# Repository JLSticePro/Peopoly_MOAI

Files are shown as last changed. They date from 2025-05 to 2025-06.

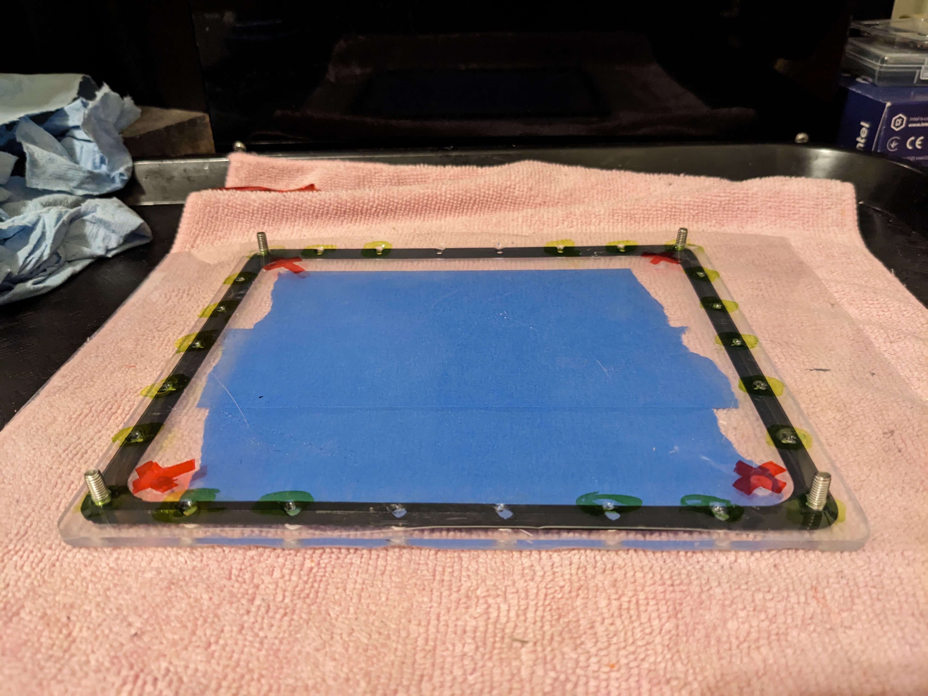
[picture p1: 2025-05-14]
Moai Vats/Printable FEP Vat with acrylic plate/Photos/Plate Ring FEP with 16mm corner screws.jpg

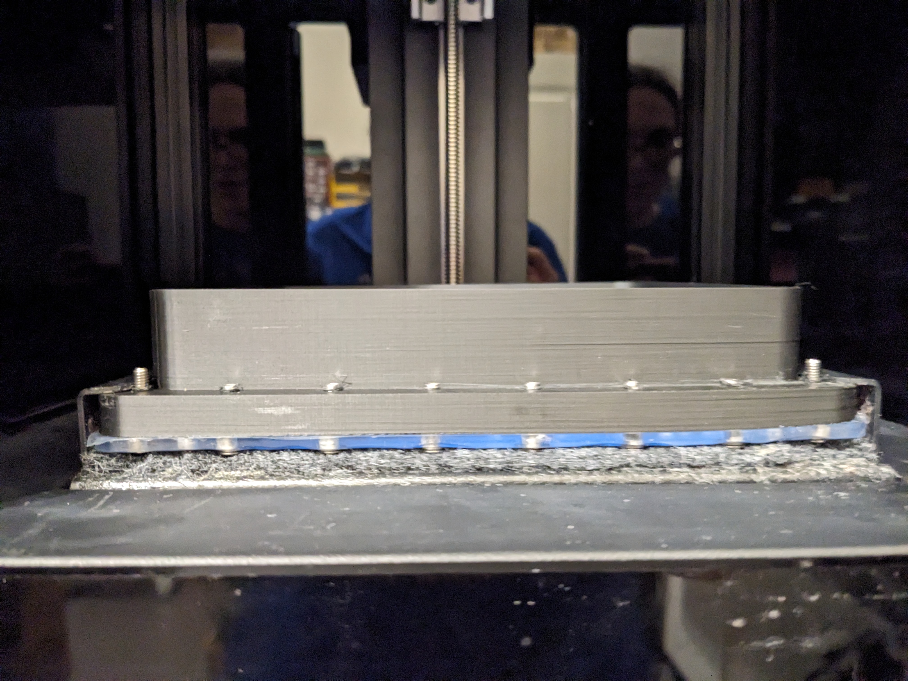
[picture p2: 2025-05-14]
Moai Vats/Printable FEP Vat with acrylic plate/Photos/A warped printed vat can not be used.jpg

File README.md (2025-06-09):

**MOAI MODEL WORK-FLOW:**
- Use ChituBox or LycheeSlicer for arranging and supporting your models.
- Export your arranged and supported model as an OBJ file.
- Open the file in MeshMixer or OrcaSlicer and repair the model
- Export the object as a new STL file. (Cura often fails with OBJ files)
- Slice using CURA 4.7 with the profiles that are included in this repository.
- Save the gcode file to the "gcode" folder on the SD card and put into the Moai.
- In "SETUP "advanced_setting" set the "XY Speed Set" for the cure speed of the resin. (Print-speed Multiplier)

**2025-06-07 New Cura Profiles** -JLS

**2025-06-05 New High-Volume Printable Film Vat** -JLS

**2025-05-11 Initial Commit** -JLS
This repository holds all cumulative files for the MOAI Laser SLA printer. 
This includes all current projects and previous developer files, provided by Peopoly, as the developer no longer works at the company and they are no longer hosting the repository. 
Files over 100MB have been removed from the older repository to meet the 100MB standard push limits, these files are older software and slicer installers.

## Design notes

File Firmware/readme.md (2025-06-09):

** ** Firmware Notes ** **

**MOAI Firmware Firmware FULL CHANGELOG (Peopoly Dev)**

V.18 (Beta4)
increase Z Follow value to allow higher up movement

V.18 (Beta3)
set PM reset distance = 0 to disable PM motor
set Zfollow to negative value for up movement

V.18 (Beta2)

V.18 (Beta)
Setting definition change
Z-Follow 0-60 each unit represents 0.1mm the range of value is (-1) to (5)
Z-Follow 0 = -1 mm movement upward during peel
Z-Follow 60 = 5 mm movement downward during peel
For recommended z-follow for general printing, it is now 30 (2mm downward movement)

New commands:
M1001 X40 ;laser power change to 40
M1002 X5 ;wait for 5 seconds before continuing
M1003 X1800 ;moving build platform arm to z-axis reset spot of 1800 (in the setting) or 180mm down from the top
M1004 X50 ;peel motion 50 has no meaning
M1005 X10 ;change Pm moto speed to 10
M1006 X3 ;change Z Motor Speed to 3
M1007 X12 ;change Z Follows (distance) to 12
M1008 X15 ;change PM Reset Position to 15
M1009 X0 ;Set HE2 port LOW -- X1 ;Set HE2 port High
M1010 X0 ;Set HE3 port LOW -- X1 ;Set HE3 port High

V1.18
Print Duration
Updated default print values
Updated calibration adjustment
Update SD card read i/o.  please print directly from root directory instead of gcode directory.
Initial layers peel speed

V1.16 changelog 2018.3.15
Compensate X/Y
This adjust X/Y for distortions.  Since Galvo/laser setup only has distorion on Y-axis, adjustment to Y-axis is only needed.
Default value for Compensate X is 100
Default value for Compensate Y is 195
Rest of settings are consistent to Firmware 1.15

V1.15 changelog 20171122 
Allow finer calibration and leveling
- X / Y Size range increase from 400 to 1000.  What was 360 is now 900
- Default recommended value is set. Laser is at 58. PM and Z follow motor speed has been reduced as well as Tilt distance
- Laser does not fire when user adjust value in the setting
- User can now immediately cancel a print and it will followed with a peel action before raising the build plate to reduce peel force

V1.14 changelog 2017.09.25 
Allow finer calibration and leveling
- X / Y Size range increase from 100 to 400.  What was 90 is now 360
- Z Reset Position range, increase from 200 to 2000.  What was 188 is now 1880
- Z-follow can now be 0

V1.1x
>enter settings,  XY size is 4 times of recorded value. Z Reset Position is 10 times of the recorded value. Make sure you updated everything to recorded settings

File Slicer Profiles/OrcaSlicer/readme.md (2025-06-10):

**Peopoly Moai for OrcaSlicer**

(Do once - All) Import the "Peopoly_Moai.orca_printer" file into OrcaSlicer
(Do once - Linux or Mac) Copy "Peoploly_Moai_gCode_Processor.py" into your OrcaSlicer "Resources" folder
(Do once - Linux or Mac) Open OrcaSlicer, add the path to the .py script in "Process" "Others" "Post-processing Scripts" for the solid and hollow profiles, then save the profiles. Orcaslicer will process the gcode automatically when you export the gCode file.
(Do once - MS Windows) Install Python to Windows. Copy "Peoploly Moai gCode Processor.py" into your gCode or models folder.

**Work-Flow:**
For most resin-type models:
- Arrange, support, and hollow your models in a resin tool such as LycheeSlicer or ChituBox 
- Export the model as an .obj or .stl file
- Import the model into OrcaSlicer onto the Moai plate
- RUN "FIX MODEL" as the resin tools leave broken non-manifold edges.
- Choose solid profile if you pre-hollowed the model
- Choose hollow profile for regular FDM models, or chunky models directly on the plate. 
- Slice the model and review
- Save the gCode to a file 
  - Mac and Linux can process the py code during the file save.
  - Windows you will need to drag and drop the .gCode file onto the .py code file to run the script.
- Put into the "gcode" folder of a properly formatted FAT32 SD card and print!

**Set speed multiplier for your resin conditions**
One profile (width, height, speed ratios) should work for all resins. Instead of adjusting print speed in the slicer, adjust the speed multiplier on the Moai to match the cure speed of the installed resin. Cure speeds are dependent on material, transparency, and temperatures and are outside the scope of the slicer release. You will have to experiment with your materials. Testing shows that old slow resins print around x5 speed, fast modern resins can print upwards of x40 speed, With most resins curing around the x20 to x30 range.

**Machine settings recommendations:*
Use "Laser Power" of around "60" or less for 64u dot size / line width, and 50u layer height max.
Use "Laser Power" of around "50" or less for 50u dot size / line width, and 40u layer height max.

**Use Lift to Peel for Film-based Vats**
Set "XY Speed Set" (print speed multiplier) x"5" to x"50" to match the resin cure speed.
Set "Z initial speed" (Z Lift Speed) "5" to "10" depending on your resin viscosity.
Set "Z moto speed" (Z Return Speed) "15" to "30" depending on your resin viscosity.
Set "PM initial speed" (Tilt Peel Speed) to "0". 
Set "PM moto Speed" (Tilt Peel Speed) to "0". 
Set "Z Follows" (Z Lift Height) "-300" for 3mm of lift to release layer from film.
Set "PM Reset Position" (Tilt Peel Distance) to "0" to disable vat tilting.

**Version Notes:**
1.0 (Release) 2025-06-09 JLS
OrcaSlicer base printer, material, and slicer profiles created
Starter profiles provided for 50 micron printing, solid or hollow.
Python script written for post-processing of gcode from Orca or Cura to make Moai compatible.

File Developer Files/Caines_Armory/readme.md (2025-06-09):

**Caine's Armory**
Moai Development Files and Links

**Files and models on Thingiverse**
https://www.thingiverse.com/cainesarmoury/designs

**Levelling using dial indicator and never level again!**
https://www.youtube.com/watch?v=9CA3qK5JQfQ

**Better calibration guide - center galvos to the build plate!**
https://www.youtube.com/watch?v=BZ6lHGUWf1s

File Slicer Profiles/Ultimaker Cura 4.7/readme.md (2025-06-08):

Ultimaker Cura 4.7
Peopoly Moai 130

Two methods for updating the machine, extruder, and layer profiles:

"profiles" folder: Import these profiles into Cura as Custom profiles

"resources" folder: Copy this folder into your Cura program folder to replace the default profiles

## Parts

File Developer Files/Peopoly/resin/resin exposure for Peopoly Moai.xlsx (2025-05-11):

Suggested Moai Exposure Settings for UV Resins
Note: | These are recommended values based on our experience or user feed but are not absolute
 | Individual factors such as temperature, leveling and others affects how resin cures, please adjust values as needed for your situation.
 | To learn about to find optimal exposure, please use this guide:
 | https://peopoly.dozuki.com/Guide/Moai+-+How+to+find+resin+exposure+time/4
Brand | Type | Color | Layer Height (um) | Moai Laser Setting | Moai 200 Laser Setting | Print Speed | Initial layer height (um) | Initial layer print speed | initial slower layer | Contributer | Notes
Peopoly | Moai Resin | Gray Blue Red | 100 | 57-58 | 58 | 85 | 100 | 5 | 2 | Peopoly | Recommend update to new firmware setting of pm motor speed 20 and z motor speed 6. please refer http://wiki.peopoly.net/doku.php?id=moai:firmware&s[]=firmware
Peopoly | Moai Resin | Gray Blue Red | 50 | 57-58 | 58 | 130 | 100 | 5 | 2 | Peopoly | Recommend update to new firmware setting of pm motor speed 20 and z motor speed 6. please refer http://wiki.peopoly.net/doku.php?id=moai:firmware&s[]=firmware
Peopoly | Moai Resin | Gray Blue Red | 25 | 57-58 | 58 | 170 | 100 | 5 | 2 | Peopoly | Recommend update to new firmware setting of pm motor speed 20 and z motor speed 6. please refer http://wiki.peopoly.net/doku.php?id=moai:firmware&s[]=firmware
Peopoly | Moai Resin | Black White | 100 | 58-59 | 59 | 85 | 100 | 5 | 2 | Peopoly | Recommend update to new firmware setting of pm motor speed 20 and z motor speed 6. please refer http://wiki.peopoly.net/doku.php?id=moai:firmware&s[]=firmware
Peopoly | Moai Resin | Black White | 50 | 58-59 | 59 | 130 | 100 | 5 | 2 | Peopoly | Recommend update to new firmware setting of pm motor speed 20 and z motor speed 6. please refer http://wiki.peopoly.net/doku.php?id=moai:firmware&s[]=firmware
Peopoly | Moai Resin | Black White | 25 | 58-59 | 59 | 170 | 100 | 5 | 2 | Peopoly | Recommend update to new firmware setting of pm motor speed 20 and z motor speed 6. please refer http://wiki.peopoly.net/doku.php?id=moai:firmware&s[]=firmware
Peopoly | Moai Resin | Clear, Neon Green | 50 | 57 | 57 | 130 | 100 | 5 | 2 | Peopoly | Recommend update to new firmware setting of pm motor speed 20 and z motor speed 6. please refer http://wiki.peopoly.net/doku.php?id=moai:firmware&s[]=firmware
Peopoly | Moai Resin | Clear, Neon Green | 100 | 57 | 57 | 85 | 100 | 5 | 2 | Peopoly | Recommend update to new firmware setting of pm motor speed 20 and z motor speed 6. please refer http://wiki.peopoly.net/doku.php?id=moai:firmware&s[]=firmware
Peopoly | Moai Resin | Clear, Neon Green | 25 | 57 | 57 | 170 | 100 | 5 | 2 | Peopoly | Recommend update to new firmware setting of pm motor speed 20 and z motor speed 6. please refer http://wiki.peopoly.net/doku.php?id=moai:firmware&s[]=firmware
Peopoly | Next (HiTemp) | Flesh/Skin/Grey | 100 | 51 | 51 | 85 | 100 | 5 | 2 | some users print at 50, it is best to use a sharp object to remove print due to high hardness
Peopoly | Next (HiTemp) | Flesh/Skin/Grey | 50 | 51 | 51 | 130 | 100 | 5 | 2 | some users print at 50, it is best to use a sharp object to remove print due to high hardness
Peopoly | Next (HiTemp) | Flesh/Skin/Grey | 25 | 51 | 51 | 170 | 100 | 5 | 2 | some users print at 50, it is best to use a sharp object to remove print due to high hardness
Peopoly | Next (HiTemp) | Clear | 100 | 54 | 54 | 85 | 100 | 5 | 2 | Nex Clear is slightly softer than other Nex
Peopoly | Next (HiTemp) | Clear | 50 | 54 | 54 | 130 | 100 | 5 | 2 | Nex Clear is slightly softer than other Nex
Peopoly | Next (HiTemp) | Clear | 25 | 54 | 54 | 170 | 100 | 5 | 2 | Nex Clear is slightly softer than other Nex
Peopoly | Tough | Clear | 100 | 51 | 51-52 | 85 | 100 | 5 | 2 | pm motor speed 15, z motor speed, it is print to the left side to reduce peel force. use thicker support/tips
Peopoly | Tough | Clear | 50 | 51 | 51-52 | 130 | 100 | 5 | 2 | pm motor speed 15, z motor speed, it is print to the left side to reduce peel force. use thicker support/tips
Peopoly | Tough | Clear | 25 | 51 | 51-52 | 170 | 100 | 5 | 2 | pm motor speed 15, z motor speed, it is print to the left side to reduce peel force. use thicker support/tips
Peopoly | Deft | Grey, White | 100 | 50 |  | 85 | 100 | 5 | 2 | use same slicing profiles as regular Moai model resin, just dial down the power
Peopoly | Neo | all colors | 100 | 49 |  | 85 | 100 | 5 | 2 | use same slicing profiles as regular Moai model resin, just dial down the power
Nextdent | Cr & Br |  | 100 | 53 |  | 85 | 100 | 5 | 2 | D. Lee
Nextdent | Cr & Br |  | 50 | 53 |  | 130 | 100 | 5 | 2 | D. Lee
Nextdent | Cr & Br |  | 25 | 53 |  | 170 | 100 | 5 | 2 | D. Lee
Nextdent | SG |  | 100 | 54 |  | 85 | 100 | 5 | 2 | D. Lee
Nextdent | SG |  | 50 | 54 |  | 130 | 100 | 5 | 2 | D. Lee
Nextdent | SG |  | 25 | 54 |  | 170 | 100 | 5 | 2 | D. Lee
Nextdent | Ortho Clear |  | 100 | 49 |  | 75 | 100 | 5 | 2 | chadfroe
Nextdent | Ortho Clear |  | 50 | 49 |  | 130 | 100 | 5 | 2 | chadfroe
Nextdent | Ortho Clear |  | 25 | 49 |  | 170 | 100 | 5 | 2 | chadfroe
Nextdent | C&B MFH |  | 100 | 50 |  | 90 | 100 | 5 | 2 | chadfroe
Nextdent | C&B MFH |  | 50 | 50 |  | 130 | 100 | 5 | 2 | chadfroe
Nextdent | C&B MFH |  | 25 | 50 |  | 170 | 100 | 5 | 2 | chadfroe
Moonray | SG | Transparent | 100 | 50 |  | 85 | 100 | 5 | 2 | David WH
Moonray | SG | Transparent | 50 | 50 |  | 130 | 100 | 5 | 2 | David WH
Moonray | SG | Transparent | 25 | 50 |  | 170 | 100 | 5 | 2 | David WH
MakerJuice | Waxcat | Orange | 100 | 59 |  | 85 | 100 | 5 | 2 | Bobby A | Not as easy to cast cleanly
MakerJuice | Waxcat | Orange | 50 | 59 |  | 130 | 100 | 5 | 2 | Bobby A | Not as easy to cast cleanly
MakerJuice | Waxcat | Orange | 25 | 59 |  | 170 | 100 | 5 | 2 | Bobby A | Not as easy to cast cleanly
MakerJuice | G+ | Blue | 100 | 54 |  | 85 | 100 | 5 | 2 | PaulY | very high shrinkage
MakerJuice | G+ | Blue | 50 | 54 |  | 130 | 100 | 5 | 2 | PaulY | very high shrinkage
MakerJuice | G+ | Blue | 25 | 54 |  | 170 | 100 | 5 | 2 | PaulY | very high shrinkage
MakerJuice | SF | Red | 100 | 53 |  | 85 | 100 | 5 | 2 | CCox | hard to fully cured. user reported random tiny holes may appear, very thin and suspect to pigment settling and bubbles
MakerJuice | SF | Red | 50 | 53 |  | 130 | 100 | 5 | 2 | CCox | hard to fully cured. user reported random tiny holes may appear, very thin and suspect to pigment settling and bubbles
MakerJuice | SF | Red | 25 | 53 |  | 170 | 100 | 5 | 2 | CCox | hard to fully cured. user reported random tiny holes may appear, very thin and suspect to pigment settling and bubbles
Funtodo | Snow White | White | 100 | 54 |  | 85 | 100 | 5 | 2 | David WH
Funtodo | Snow White | White | 50 | 54 |  | 130 | 100 | 5 | 2 | David WH
Funtodo | Snow White | White | 25 | 54 |  | 170 | 100 | 5 | 2 | David WH
Funtodo | Castable | pink | 100 | 48 |  | 150 | 100 | 5 | 2 | Bobby A | quick damages to resin
Funtodo | Castable | pink | 50 | 48 |  |  | 100 | 5 | 2 | Bobby A | quick damages to resin
Funtodo | Castable | pink
Dreve | FotoDent Model | White | 100 | 54 |  | 85 | 100 | 5 | 2 | David WH
Dreve | FotoDent Model | White | 50 | 54 |  | 130 | 100 | 5 | 2 | David WH
Dreve | FotoDent Model | White | 25 | 54 |  | 170 | 100 | 5 | 2 | David WH
Dreve | FotoDent SG | Transparent | 100 | 52 |  | 85 | 100 | 5 | 2 | David WH
Dreve | FotoDent SG | Transparent | 50 | 52 |  | 130 | 100 | 5 | 2 | David WH
Dreve | FotoDent SG | Transparent | 25 | 52 |  | 170 | 100 | 5 | 2 | David WH
Spot-A | HT | Yellow | 100 | 57 |  | 85 | 100 | 5 | 2 | William L
Spot-A | HT | Yellow | 50 | 57 |  | 130 | 100 | 5 | 2 | William L
Spot-A | HT | Yellow | 25 | 57 |  | 170 | 100 | 5 | 2 | William L
Siraya Tech | Fast | Grey, White, Black, Green, Creamy | 100 | 50 |  | 85 | 100 | 5 | 2
Siraya Tech | Simple | all colors | 100 | 49 |  | 85 | 100 | 5 | 2
 |  | *warning
 |  | photocentric tough | doesn't print well and have problem stay on the plate
Printing Guide:
Nex HiTemp Resin |  | http://wiki.peopoly.net/doku.php?id=moai:nexresin
Tough V2 Resin |  | http://wiki.peopoly.net/doku.php?id=moai:toughresin
Difficult to print / softer resin can use Tough V2 guide as guideline

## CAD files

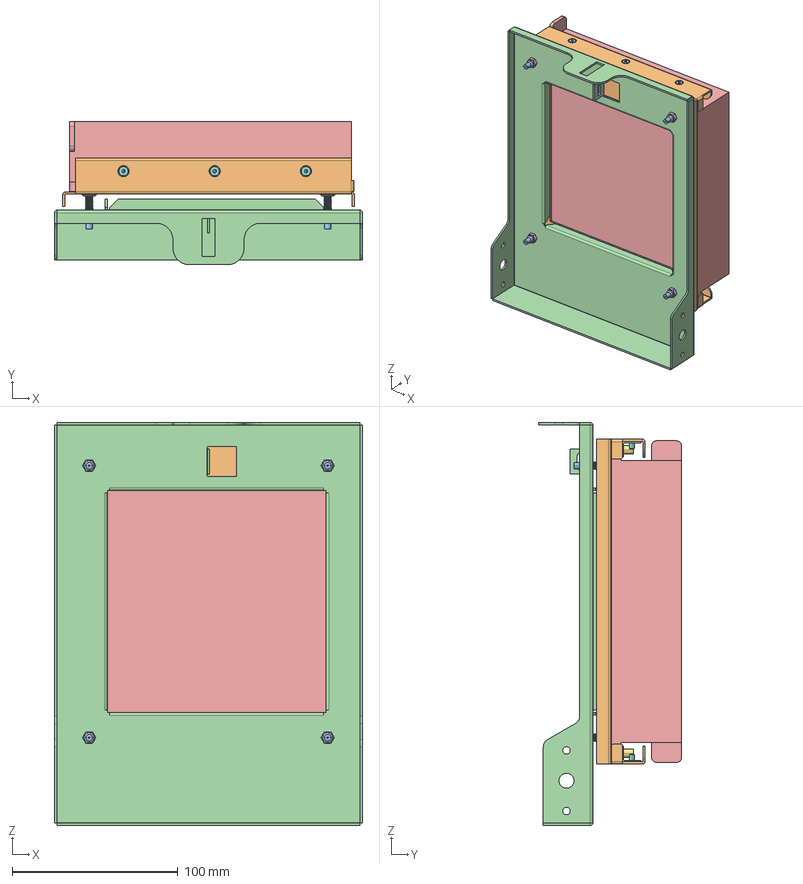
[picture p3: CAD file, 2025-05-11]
Developer Files/Peopoly/reference/moai-leveling-mechaism/leveling_asm.stp
185.9 x 86.5 x 243.0 mm
TIAOPINGHUODONGBAN
ZHUANZHOUBAN
YETICAO
CBTN4-T x 4
YETICAODINGWEIJIAN
CHENTOUM3-6 x 6
TANHUANG-X_MIR x 4
PRT0001

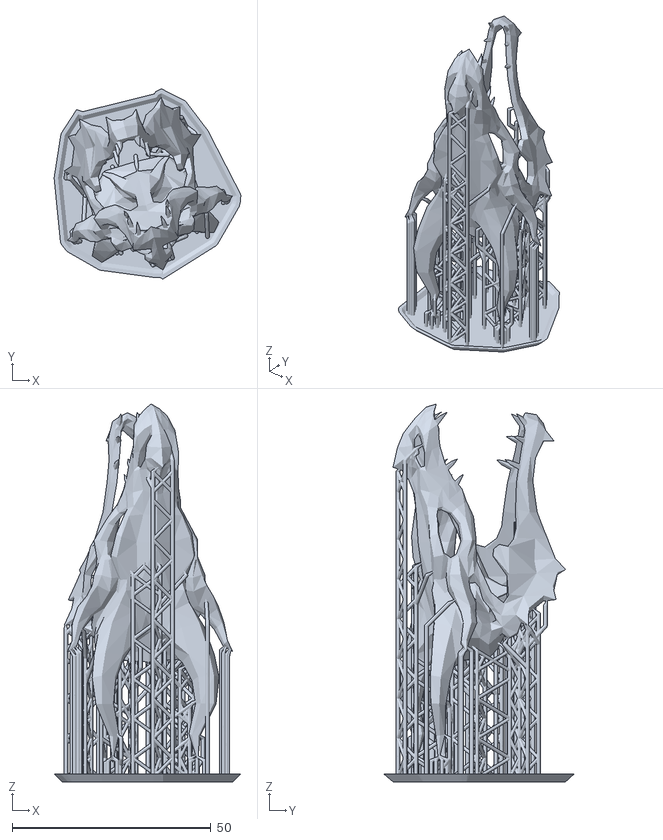
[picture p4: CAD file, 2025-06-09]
Developer Files/JLSticePro/Moai Test Files/dragon_skull.stl
47.0 x 47.9 x 95.2

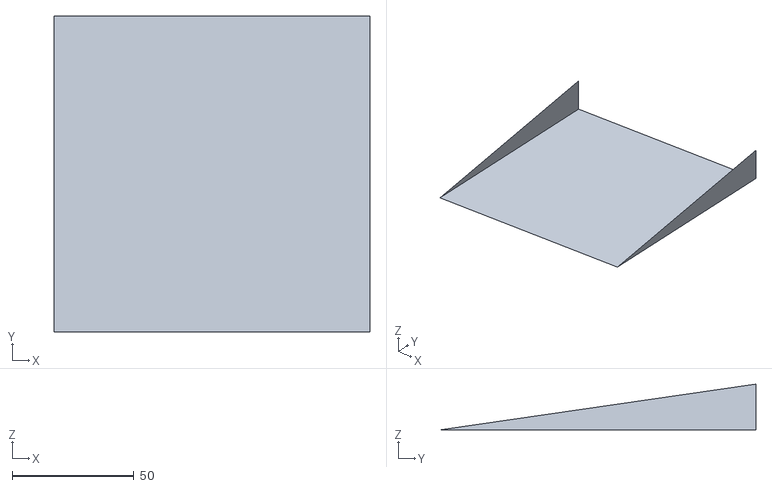
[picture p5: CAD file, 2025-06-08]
Developer Files/JLSticePro/Slicer Profile Tuning/Ultimaker Cura 4.7 (originals)/resources/meshes/moai.obj
130.0 x 130.0 x 18.8

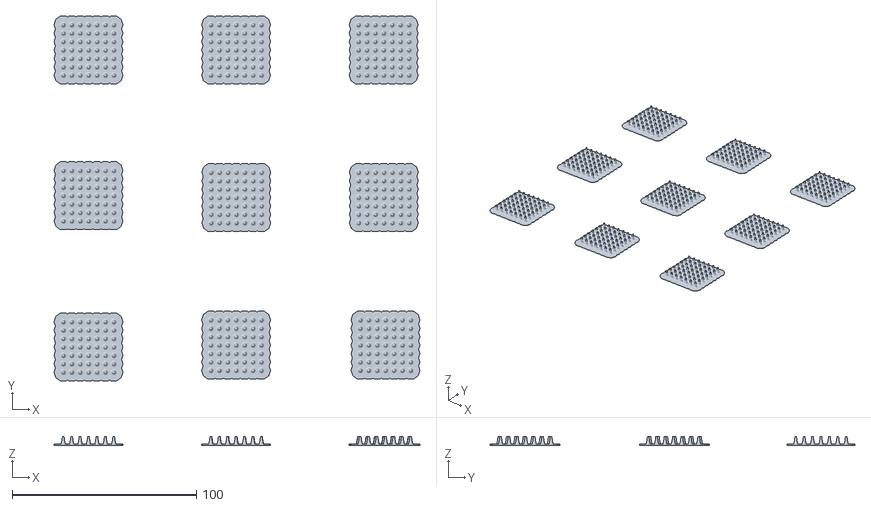
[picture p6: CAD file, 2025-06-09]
Developer Files/Peopoly/prints/200-leveling-big.stl
198.4 x 197.9 x 4.95

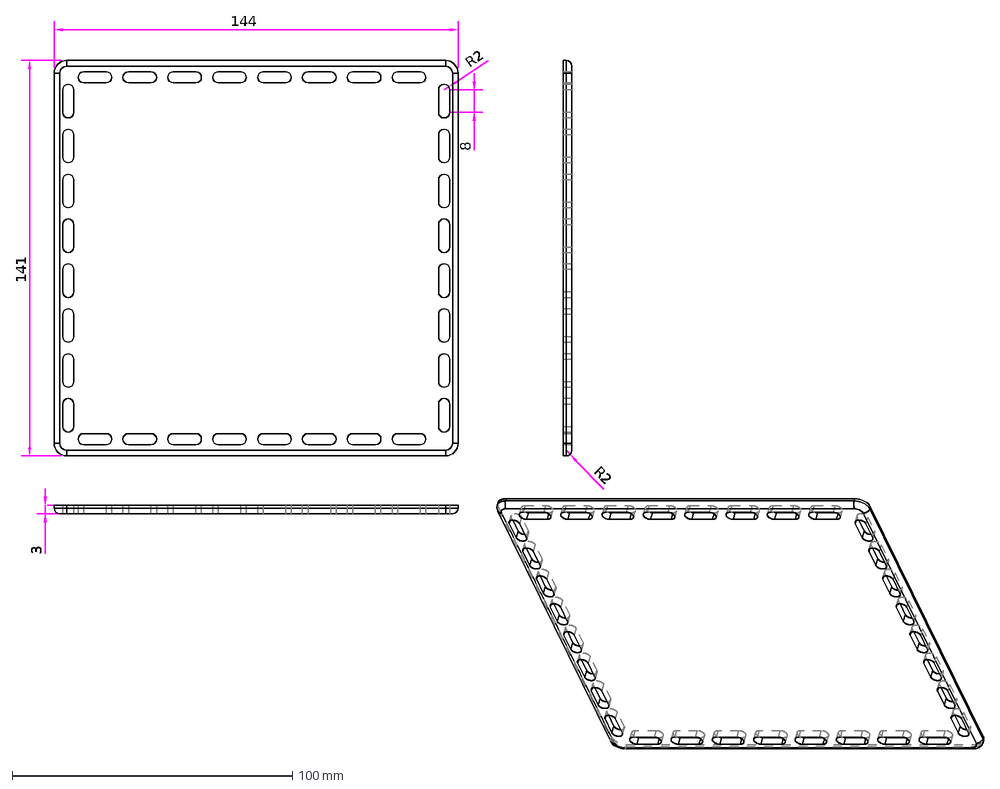
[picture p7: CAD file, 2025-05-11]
Developer Files/Peopoly/reference/FEP-vat-a·cryl·ic.dxf
144
141
3
R2
8

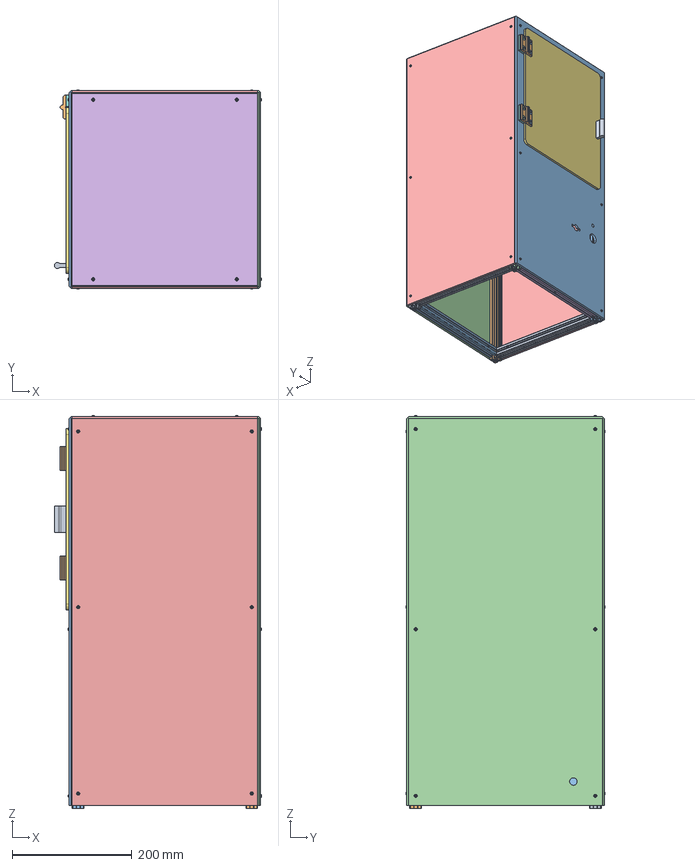
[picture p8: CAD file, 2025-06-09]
Developer Files/Peopoly/reference/moai-external-structual/moai-external-structual.stp
346.6 x 333.3 x 656.7 mm
MSBR-322
MSBR-321
MSBR-320
MSBR-319
MSBR-318
MSBR-317
MSBR-316
MSBR-315
MSBR-314
MSBR-313
MSBR-312
MSBR-311
MSBR-310
MSBR-309
MSBR-308
MSBR-307
MSBR-306
MSBR-305
MSBR-304
MSBR-303
MSBR-302
MSBR-301
MSBR-300
MSBR-299
MSBR-298
MSBR-297
MSBR-296
MSBR-295
MSBR-294
MSBR-293
MSBR-292
MSBR-291
MSBR-290
MSBR-289
MSBR-288
MSBR-287
MSBR-286
MSBR-285
MSBR-284
MSBR-283
MSBR-282
MSBR-281
MSBR-280
MSBR-279
MSBR-278
MSBR-277
MSBR-163
MSBR-162
MSBR-161
MSBR-160
MSBR-158
MSBR-157
MSBR-156
MSBR-155
MSBR-154
MSBR-153
MSBR-152
MSBR-41
MSBR-40
MSBR-39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

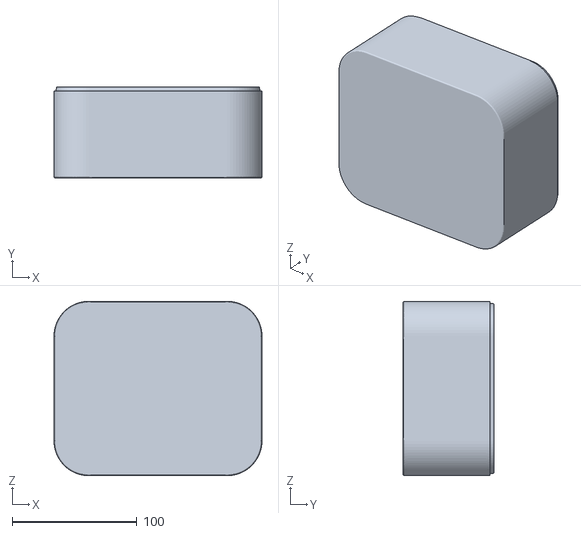
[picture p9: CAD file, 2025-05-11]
Developer Files/Peopoly/reference/Peopoly UV Box/Peopoly UV Box/id_uv_box_02.stl
167.0 x 73.0 x 140.0

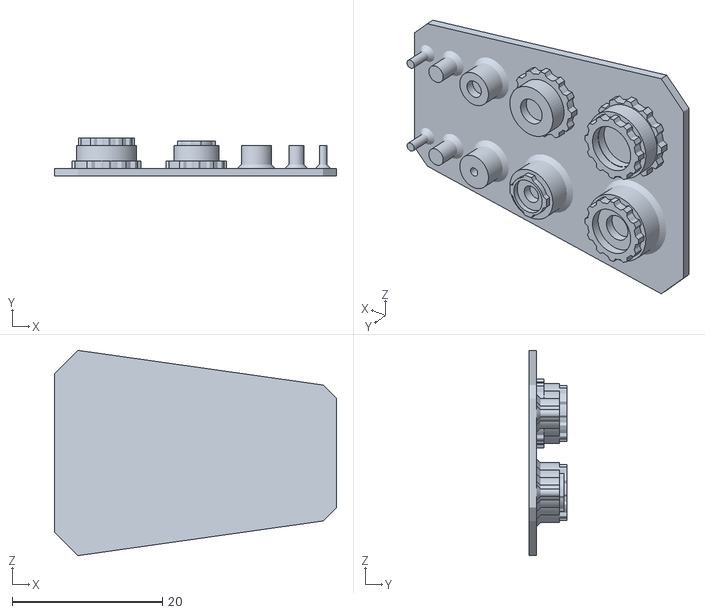
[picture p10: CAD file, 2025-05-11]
Developer Files/Peopoly/Slicer_Profiles/g0 test/cylinderTabs_02.STL
37.6 x 5.00 x 27.4

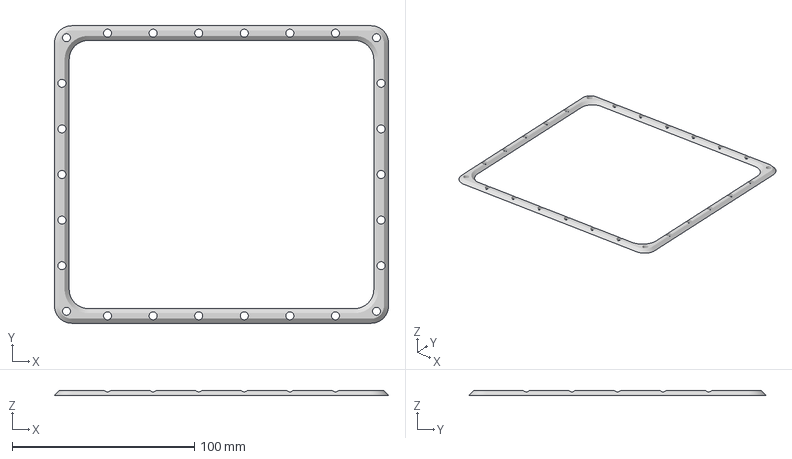
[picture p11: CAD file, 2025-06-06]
Moai Vats/Printable FEP Vat with acrylic plate/FEP_VAT_V12/Stretch Ring 2.5mm.3mf
183.1 x 163.1 x 2.50 mm

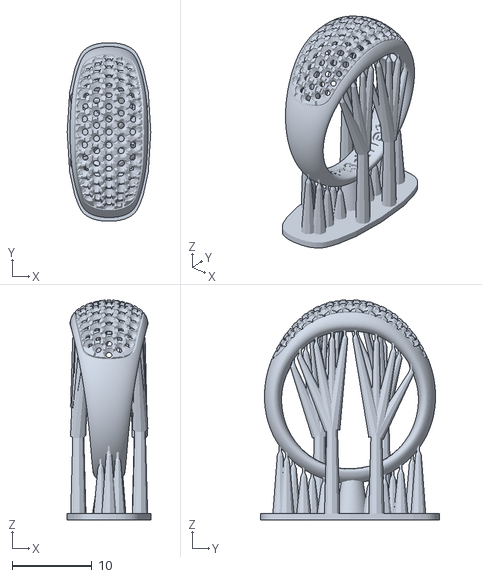
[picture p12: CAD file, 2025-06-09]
Setup Instructions/Peopoly/ring-test.stl
10.5 x 22.4 x 27.7

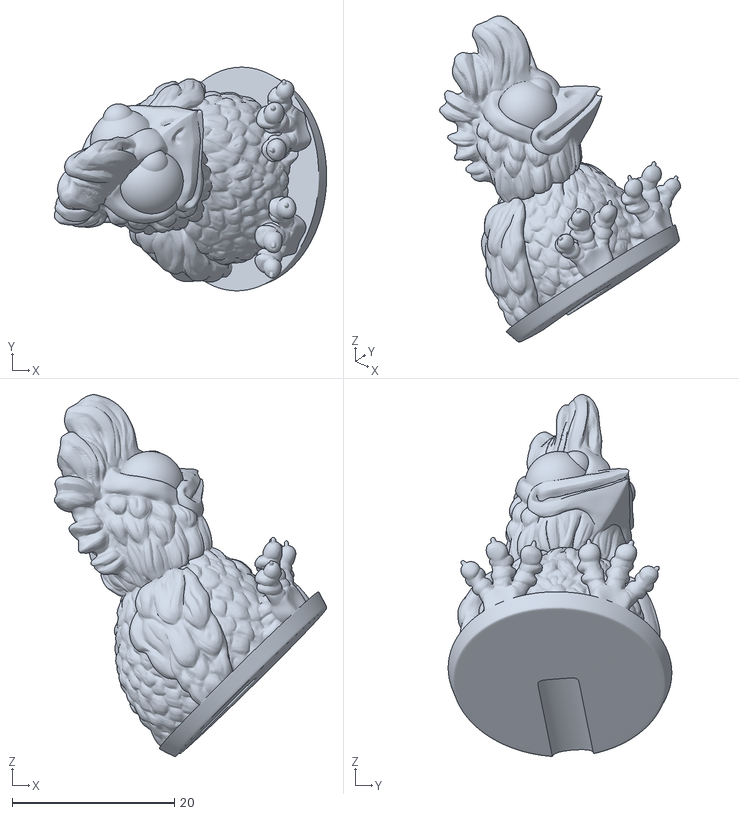
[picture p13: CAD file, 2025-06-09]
Developer Files/JLSticePro/Moai Test Files/poussin.stl
33.6 x 27.6 x 44.7

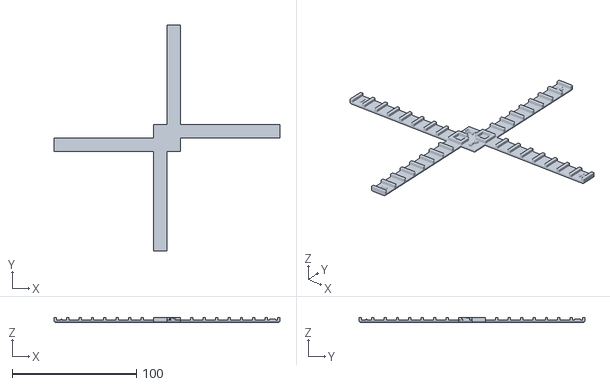
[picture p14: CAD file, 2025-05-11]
Developer Files/Peopoly/prints/200-asuracalibration.stl
182.0 x 182.0 x 4.00

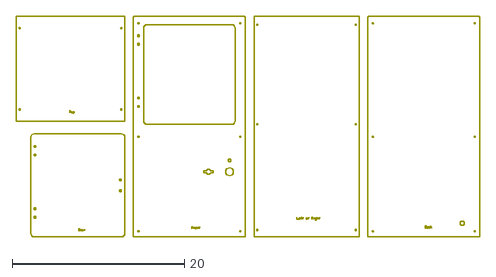
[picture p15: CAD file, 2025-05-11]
Developer Files/Peopoly/reference/moai-external-structual/Moai-Flat-Panels-Inch.dxf
53.8 x 25.6

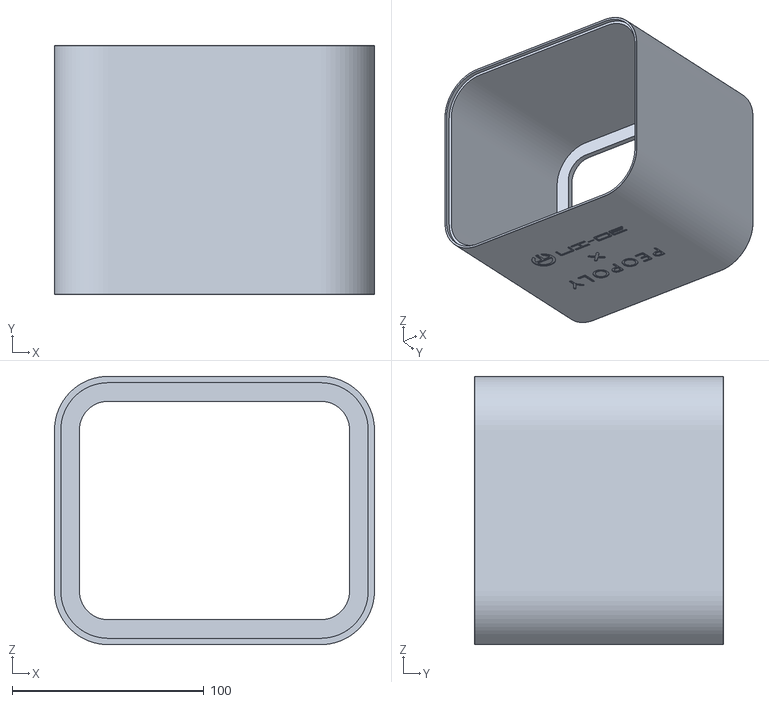
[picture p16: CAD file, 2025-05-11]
Developer Files/Peopoly/reference/Peopoly UV Box/Peopoly UV Box/id_uv_box_01.stl
167.0 x 130.0 x 140.0

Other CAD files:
Moai Vats/Peopoly Vats Reference/Moai_vat.dwg
Developer Files/Peopoly/reference/Moai vat.dwg
Developer Files/JLSticePro/Moai Test Files/dragon_skull.obj
Developer Files/Peopoly/Slicer_Profiles/g0 test/cylinderTabs.STL
Developer Files/Peopoly/Slicer_Profiles/g0 test/cylinderTabs03.stl
Developer Files/Peopoly/prints/200-asuracalibration-198.stl
Developer Files/Peopoly/prints/20mm-resin-saver-cube.stl
Developer Files/Peopoly/prints/A11.stl
Developer Files/Peopoly/prints/B11.stl
Developer Files/Peopoly/prints/C11.stl
Developer Files/Peopoly/prints/D11.stl
Developer Files/Peopoly/prints/Z_30mm.stl
Developer Files/Peopoly/prints/a.stl
Developer Files/Peopoly/prints/asura-calib-print-Moai.stl
Developer Files/Peopoly/prints/b.stl
Developer Files/Peopoly/prints/c.stl
Developer Files/Peopoly/prints/cross-center.stl
Developer Files/Peopoly/prints/d.stl
Developer Files/Peopoly/prints/e.stl
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

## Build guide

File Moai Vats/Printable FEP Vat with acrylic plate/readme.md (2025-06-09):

MOAI 130 FEP Vat by JLS

This vat is designed to use minimal parts and only simple hand-tools to make and assemble.
No modification of the printer mechanism required, only add felt strip to grip new vat.

Tools you will need:
	FDM / FFF 3D Printer with 0.4mm or 0.6mm nozzle
	Drill (hand or powered)
	Drill bits: 3mm, 4mm or 1/8 inch, 5/32 inch
	COARSE sandpaper
	Masking tape (BLUE removeable is preferred)
	Metal putty knife
	Simple pliers
	Utility or Razor knife
	Hex wrenches to match machine screws
	Small, pointy Phillips or J1 screwdriver (4mm or smaller)
	Microfiber cloth at least as large as the vat.

Parts you will need:
	( 1) FEP sheet large enough to extend beyond the edges of the new vat
	(26) M4 x 12mm BUTTON HEAD stainless steel machine screws and M4 Washers
	(1m) 12mm x 4mm (1/2 x 5/32) felt strip and contact adhesive, or use a self-adhesive strip
		(alternative sizes acceptable) (commonly called weather stripping)

Preparing the acrylic build surface:
------------------------------------
	
You may use the acrylic plate from the bottom of your damaged Silicon vat for your new FEP vat.
	* You must be careful not to scratch the acrylic in the build area of the plate!
	* The edges not part of the build area can have scratches, but not raised areas when complete.
	* The bottom of the plate will be used as the new top of the plate as it's edges will be less damaged.
Acrylic plate salvage process:
	Carefully peel the PDMS / Silicone material out of the vat.
	Apply masking tape to the RESIN area inside the vat and again on the bottom side inside the ring.
	Use the pliers to break away the vertical sections of the vat.
	Use the putty knife to chip away any remaining acrylic on the edges.
	Use the putty knife to scrape the edges until flat.
	Use the coarse sandpaper to smooth the edges.
	Use the putty knife to remove the bottom ring and scrape any glue away.
	Use the sandpaper to smooth the bottom edges of the plate if needed.

You may use a new piece of 3mm clear acrylic plate. (Lexan is untested)
	* Many hardware stores can cut the acrylic to size. Take the drill guide with you!
	* You should round the corners, but they do not need to be perfectly matched to the guide.
	* Use sandpaper to buff the edges of the acrylic to prevent injury from sharp edges.

Print the drill guide:
	Thick layers, Draft quality. You will only need the part once.

Drill the holes in the acrylic plate:
	* USE LIGHT PRESSURE AND SLOW SPEED when drilling acrylic!
	Remove any old masking tape, and plastic if sheet is new.
	Cover BOTH sides of the acrylic with masking tape.
	Tape the drill guide to one side of the plate.
	Use the smaller drill to drill straight through the acrylic for all holes in the guide.
	Remove the drill guide.
	Using the larger drill bit, DRILL IN REVERSE for a few turns on BOTH SIDES of each hole.
	Using the larger drill bit, regular direction to finish drilling the holes through.
	Make sure screws slide through easily. Drill again if needed.
	Remove all chips and burrs from the holes. 
	Leave masking tape on until assembly.

Assembling the FEP VAT:
----------------------

Print the VAT parts:
	The VAT and the STRETCH RING are designed to be printed together.
	The ring functions as a print-in-place support for the recessed area under the vat.
	A SOLID print is recommended, however you may opt for 3 walls and moderate in-fill if you have warping issues with solid prints.
	Use PLA, PLA+, or Tough PLA; color does not matter.
	Do not use ABS as the resin will melt it over time!

Prepare the FEP sheet:
	* Do not remove sheet protectors or masking tape yet!
	Lay the FEP sheet on top of the acrylic plate
	* Do not puncture the four vacuum relief holes at the corners, only the four OUTER corner holes.
	Use the small screwdriver to puncture holes along the outer edge of the plate.

Assemble the VAT:
	Place a washer on each of the machine screws.
	Remove the masking tape from the acrylic plate.
	Orient the smoother side of the plate facing up. 
	Place a screw in each of the corners of the plate from the bottom, pointing upwards.
	Set the plate with four screws onto a microfiber cloth. 
	Place the STRETCH RING onto the plate (wide side down).
	Peel ONE SIDE of the FEP sheet protector off, and place that side down onto the four bolts.
	Remove the other sheet protector from the top of the FEP sheet.
	Carefully add all of the other bolts up from the bottom, through the plate, ring, and FEP sheet.
	Place the VAT part upside down.
	Take the plate with FEP sheet and flip it over.
	Place the plate and sheet assembly onto the VAT part.
	Start each screw into the VAT holes a few turns, making sure they are straight!
	PUSH the entire plate and FEP sheet down against the VAT, sliding down the screws.
	Snug the screws up to the plate, but do not tighten yet.
	Go around the plate in one direction in this pattern to tighten the screws:
	Screw, skip, skip, screw, skip, skip, screw, skip two, screw ...
	Continue around three times until screws are firm.
	Repeat again, this time bringing the screws to evenly tight.
	* Careful not to over-tighten screws! Gently proceed and repeat until everything is even!
	
Prepare the Printer for the new FEP Vat:
----------------------------------------

Preparing the Tilt-Plate in the machine:
	You will be applying four strips of felt to the large flat, rectangular surface the vat will sit on.
	Apply the side strips first, then the front and rear, covering the entire flat metal surface.

Change machine settings:
	EXTREMELY IMPORTANT: You must change the "Z-Reset Position" to "1850" and double-click to save.
	This setting is accessed via "SETUP" then "advanced_setting" then "Z-Reset Position"

Level the vat:
	* This process is different than that of the standard instructions.
	* The FELT allows a slight spring relief for the pressure of the initial layers.
	Switch the machine OFF.
	Install the new vat.
	Switch the printer ON. (warning, build plate may move!)
	Change the Z-Reset by increasing by 5 to 1855, double click to save.
	Build plate should move down into the VAT. If not repeat the setting and save again.
	Check to see if there is pressure against the FEP in the vat:
	* When the build plate is pressing on the FEP firmly enough you will feel a slight gap
	  between the top of the printed VAT and the part of sheet metal that holds it down. 
	* This gap should be just enough to feel with your finger-nail. 
	* The exact amount is not important, only that there is a slight gap caused by the pressure
	If there is no pressure and gap on any corner, return to settings and add 5 more and save.
	Repeat until you feel a pressure gap on at least two corners!
	
	Standard Build Plate:
	Remove one side of your printer enclosure.
	From under the Tilt Plate you can now adjust the level of the vat
	* You want all four corners to have similar pressure, but they do not need to be exact.
	
	Adjustable Build Plate:
	Release the tilt screws, press the plate firmly, then re-tighten the screws.
	In settings, add 5 more and save. Check the gap on four corners for proper pressure.
	
	The Pressure gap should be approximately a fingernail or less on all four corners.
	You may need to add a few points to the Z-reset as the felt ages.
	* The felt may need to be replaced eventually as it flattens over time.
	* You will not need to re-level the plate until that time.

Printer settings for the new MOAI FDM FEP VAT:
---------------------------------------------

Calibrating the surface height:
	Your new FEP sheet is now at a slightly different height than the PDMS goop. You need to re-calibrate ONCE.
	IMPORTANT: REMOVE YOUR BUILD PLATE FOR THIS TEST! FEP Vat should be installed, clean, and empty!
	Print out your handy "Calibration_Circle.PDF" IMPORTANT: Make sure scaling is set to 100% in the print menu!
	Add "P_yuan-test.gcode" to your gcode folder on your SD card.
	Run the test file as a print, and see if it matches the circle.
	If the circle is too small, increase the "X Size" and "Y Size" numbers and re-try.
	Once it's on the circle, look at the ovality:
	- If it touches on left-right but not front-back, adjust "X Size"
	- If it touches on front-back but not left-right, adjust "Y Size"
	When you have a perfect circle, you are done with calibration.

TILT (PM) and LIFT (Z) settings:
	* Start with "Initial" speeds low at first.
	* "Fast" resins will allow you to use faster "Initial" separation speeds.
	* Important Note: The negative Z_Follows value is saved, but will display "0" when returning to the menu.
	  You can see this when you attempt to change the value, it will jump to the negative number you had set.

	You may keep and use the tilt function using the default firmware settings:
	* Tested: Works with standard FEP
	- PM_Reset = 40 (tilt distance)
	- PM_Initial = 15 (tilt speed)
	- Z_Follows = 10 (FOLLOWS tilt to reduce separation forces)
	- Z_Initial = 2 (move slowly at first)

	To disable TILT and use LIFT to peel only:
	* Tested: currently unsuccessful
	- PM_Reset = 0 (disable tilt)
	- PM_Initial = 0 (disable tilt)
	- Z_Follows = -250 (NEGATIVE value results in LIFT, each -100 is 1mm of lift)
	- Z_Initial = 2 (SLOW value to prevent separation from the build plate)

	You may also experiment with partial tilt and partial lift.
	*** UNTESTED ***
	- PM_Reset = 20 (tilt distance)
	- PM_Initial = 15 (tilt speed)
	- Z_Follows = -100 (1mm Lift)
	- Z_Initial = 2 (move slowly at first)

SPEED MULTIPLIER: (Printing with different speed resins is possible from a single g-code!)
	"XY Speed SET" in "advanced_setting" multiplies the speed called in G-Code.(example: 15x 120mm/s moves the spot at 1800mm/s!)
	* The newest firmwares unlocking the speed multiplier up to 40x or 50x for high-speed resins.
	* You can use ONE print file ("PartExample_60micron") from Cura then adjust the multiplier to suit the resin.
	* Standard opaque resins might work around 5x, and some high-speed resins may work up to 40x!
	* Each of your resins will have a preferred speed range, say 12x to 15x, depending on their temperature.

LASER POWER: (Fine-tune laser DOT, EXPERIMENTAL)
	The laser power performs very well for MSLA resins around 60% and results in the spot-size arount 67 microns.
	In CURA this setting coresponds to the LINE WIDTH for your profile. The new profiles are set to 0.0067 width.
	Playing with this setting can let you make smaller prints more detailed, or larger prints faster.
	A lower laser power cures resin slower, but has a smaller spot size. You can lower line width and layer height.
	A higher laser power cures resin faster, but has a larger spot size. You can raise line width and layer height.

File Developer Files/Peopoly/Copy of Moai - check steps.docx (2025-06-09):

Moai Calibration test

These are the steps in the order which you will do:

1. Power On
2. Galvo Scanning Test
3. Leveling

Please do not pour resin into vat until the instruction tell you so or it will make testing more difficult.

Moai is shipped with galvos and Plate calibrated.

To make sure everything is still working after delivery, we will run three tests:

DO NOT INSTALL BUILD PLATE OR PUT ANY RESIN INTO VAT for calibration test

1. Power on Check  Click the Power Switch on the Front Panel to Turn on the Machine (pic)  Two things to look for here: - Z Axis is raised to the top of the rod before stopping - The Plate will perform a tilt action and resume to level position  You should see this screen when Moai is ready:

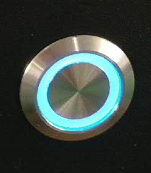
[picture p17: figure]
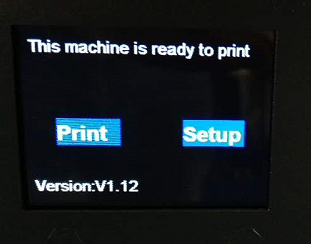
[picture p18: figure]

2. Setting check Use the Control Knob above the Power Switch to move between “Print” and “Setup”

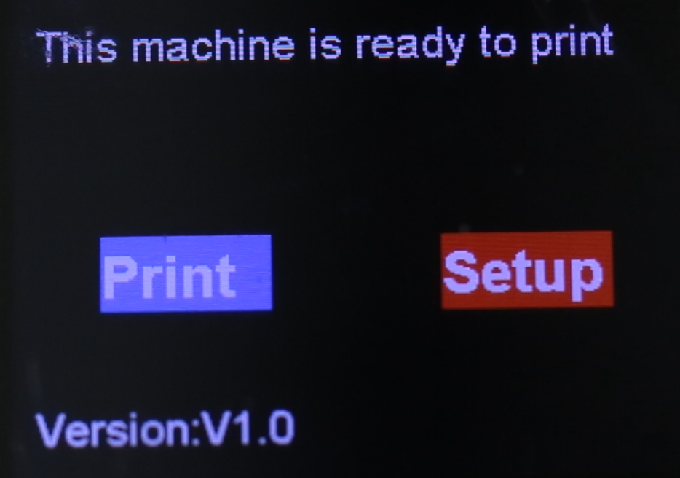
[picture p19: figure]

Press the knob to enter “Setup” (Double press to go back)

Please check your setting and adjust to match:

If not, you can select and click on each entry to adjust the value to match above numbers

Then please use Control Knob to scroll down to advanced_setting

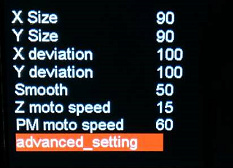
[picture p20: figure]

Check your setting against:




Laser power is a key setting. We like to set it around 61% for Moai’s resin. Please check against that. Non-Moai resin may have lower or higher laser power need.

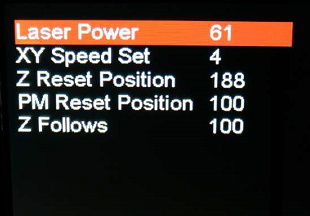
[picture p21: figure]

3. Galvo test

Please download following files

Circle marking: https://drive.google.com/open?id=0Bzke6lBHG_z5MkhwQjZ0bk5UaXM

Circle test Gcode: https://drive.google.com/open?id=0Bzke6lBHG_z5NmdFUmZENDZ0OEk

Circle market is a PDF file called: calibration-circle.pdf

Print it out and cut the square with circle out. Place it in the Vat

*note: for US/Canada user please ensure that the Calibration Circle PDF prints at 100% scale, not 91% because of the A4 to US Letter conversion. The dimensions of the printed box should be 5-1/8" (130.18mm), not 4-11/16" (119.06mm).

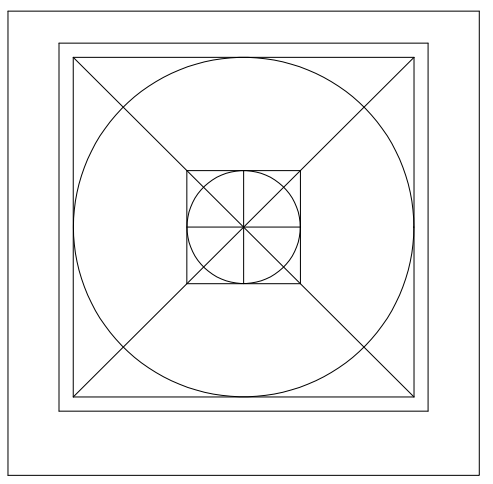
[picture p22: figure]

Extract P_yuan-test.gcode from P_yuan-test.zip and place the GCode file in directory called “gcode” in a SD card.

Insert the SD Card in the Machine:

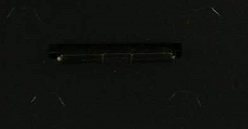
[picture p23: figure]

(reshoot)

Insert the vat with the printed calibration-circle (pic)

Select Print from the Moai’s menu and Click Confirmed.

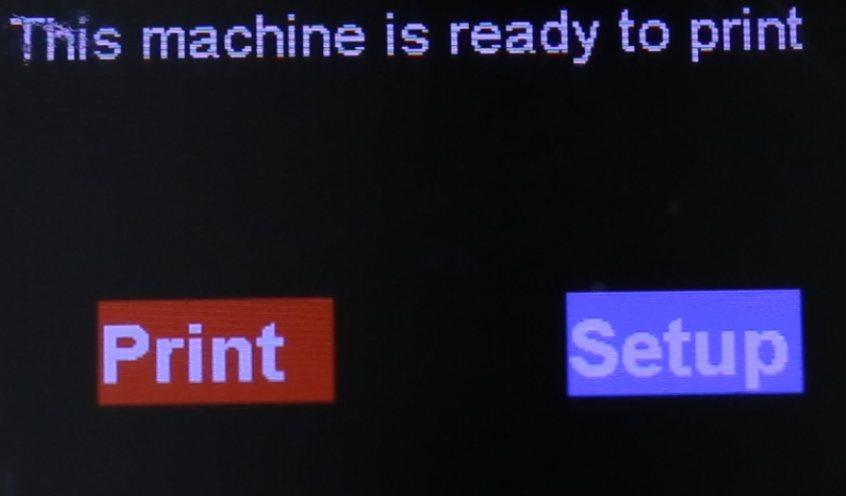
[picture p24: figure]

You should see Z-Axis drops the Build Plate arm, tilt the Vat and begin to scan like below

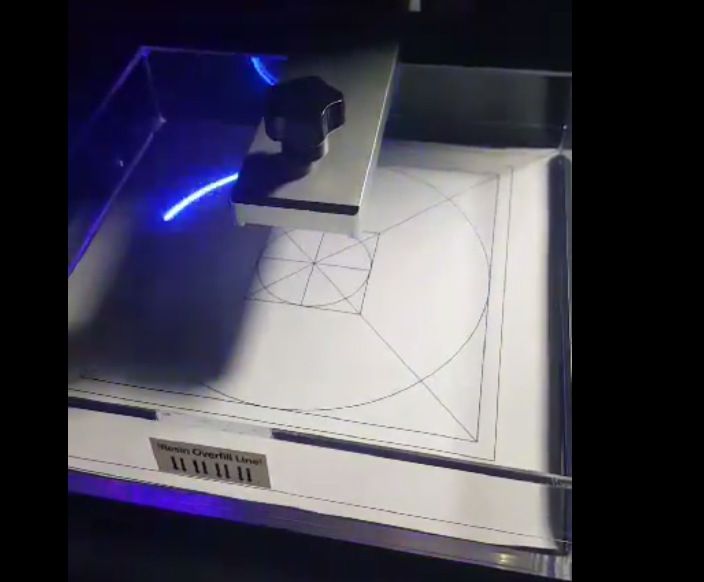
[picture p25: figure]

Video: https://youtu.be/4jeJfWrDAyI

Move the paper slightly such that the circle overlaps with the laser scanning path

Leveling

Since there are slight variation in plate and vat, it is important to level before doing any print with resin. You should do leveling when you are changing vat

Folowing instruction is for firmware 1.14 or later. If you are not on firmware 1.14 yet, please upgrade first use firmware upgrade instruction here

https://peopoly.dozuki.com/Guide/Moai+-+Firmware+Upgrade/3

Leveling for Moai is very easy to do, please follow these steps:

1. Connect the power cable before turning it on
2. Install VAT (make sure push all the way in, Do NOT pour resin)
3. Install Built Plate (Make sure the knob on top is tighten)
4. Turn Moai on
5. Use the knob to turn. Press the knob to select “Setup”

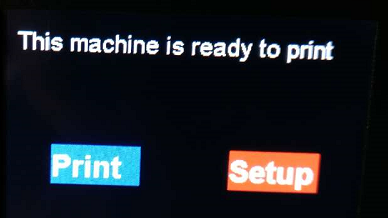
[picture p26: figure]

6. Go to the advanced_setting

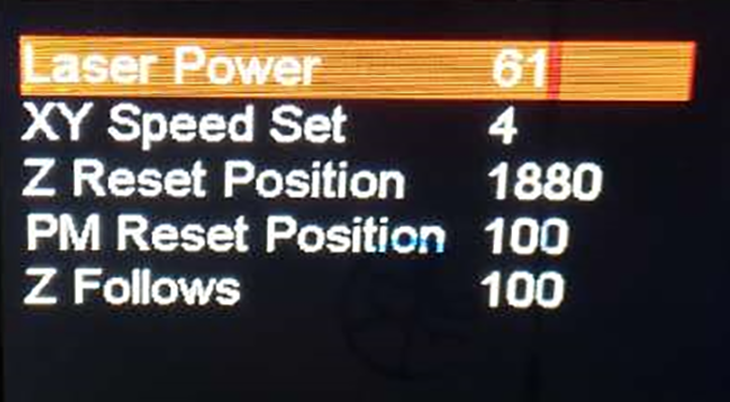
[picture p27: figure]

7. Change the Z Reset Position to 1880. Double press on the knob to exit menu. If it is already at 1880, turn to 1879 and then turn back to 1880 before double press. At this point the build Plate should began descending If there is any loud noise or Plate is going too low such it is hitting and keep press vat, press the power button off. Otherwise, just let it descent to print position.

It is very important that during step 7 that the build plate is lower into the vat before going to the next step

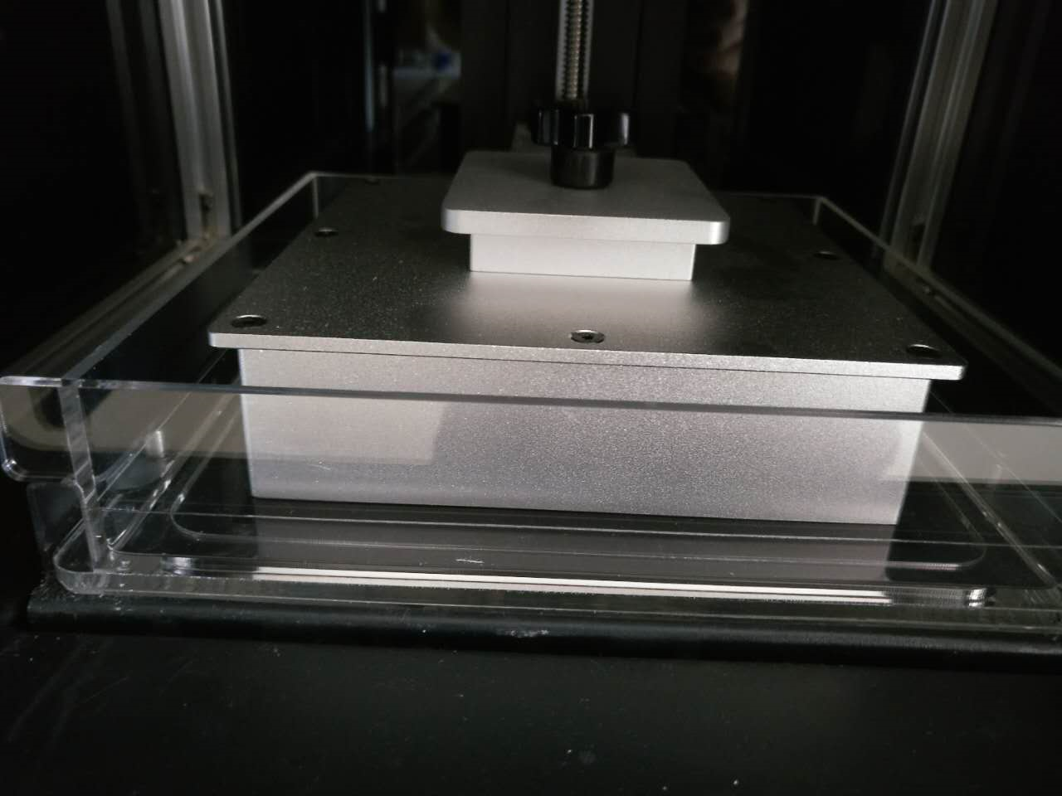
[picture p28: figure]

8. This is the key part of leveling:

There are 4 nuts/bolts right underneath of the VAT, and they look like this

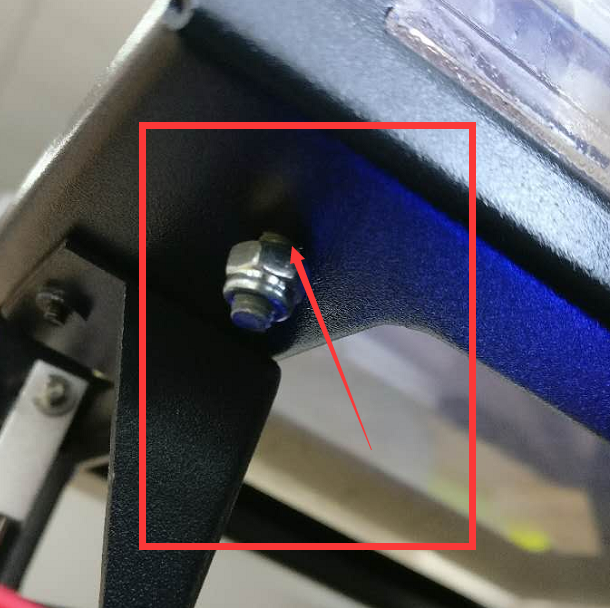
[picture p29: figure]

First, loose all four of them to a point that the nut to a point where you can see there is a gap between the nut and platform.(see above picture)

This is the tool to turn the nut when working:

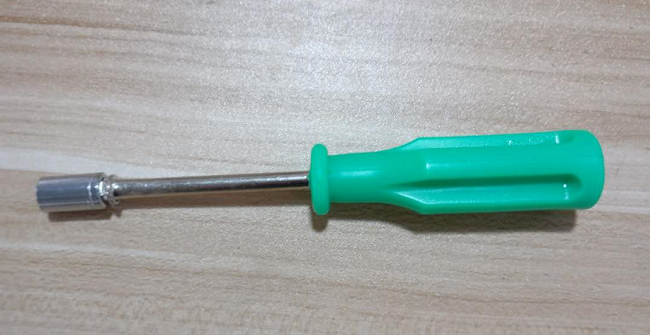
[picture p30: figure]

Then, tighten those nuts such that there is NO gap between nut and frame (nut just touching frame) but not press against it.(see below picture)

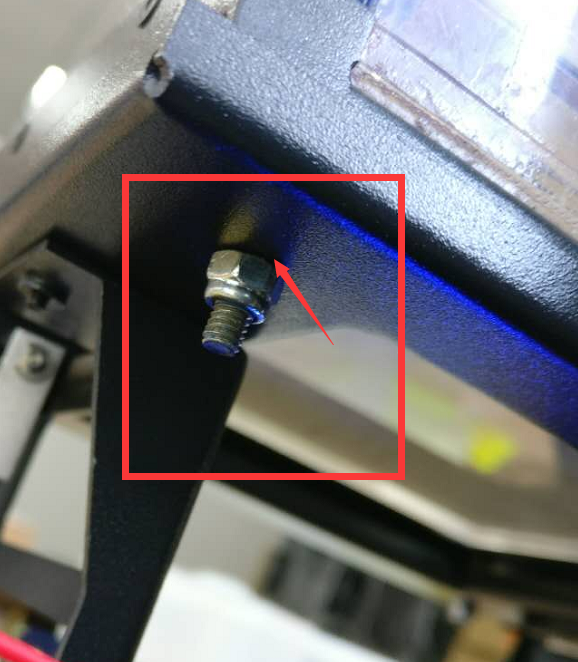
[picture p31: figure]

You can use a piece of paper to check the gap. If you can not slide the paper between the nut and the platform. It is good.

Once you are done.

Power Off the Moai by pressing power buttom

The power on Moai again

Go to Advanced settings and change Z-Reset Position from 1880 to 1877

Double press and the plate will drop down. Your Moai is now leveled.

Power Off Moai before going to next step

Leveling video: https://www.youtube.com/watch?v=652Kjil-sk8

(*need update)

For micro adjustments in case you need it:

Tightening the nut lowers the vat.

Loosening the nut raises the vat.

Test Print

- Download this test file:

https://drive.google.com/open?id=0Bzke6lBHG_z5ajN6VU1scll6QTQ

- Extract PM2_zring-test.gcode from the zip file

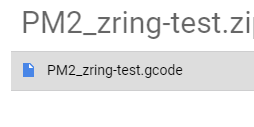
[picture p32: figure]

- Insert the included SD card into your computer

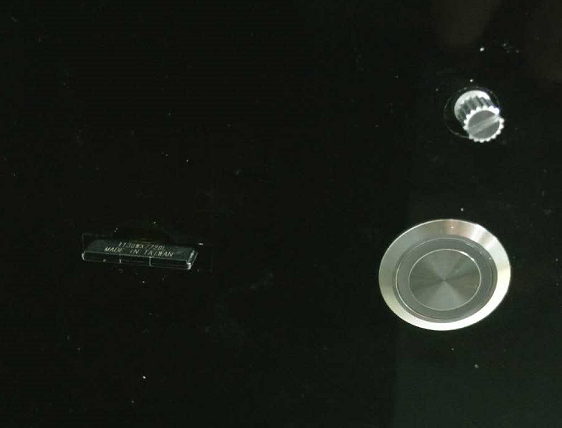
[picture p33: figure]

- Create a directory called “gcode” in the SD card
- Copy PM2_zring-test.gcode to the gcode directory created in last step
- Eject the SD card and insert it into Moai’s SD card reader
- Select Print from the Moai menu using the control knob
- Select gcode directory
- Select PM2_zring-test.gcode , and confirm to start printing

This print should last about 20 minutes and print at the B corner, see below:

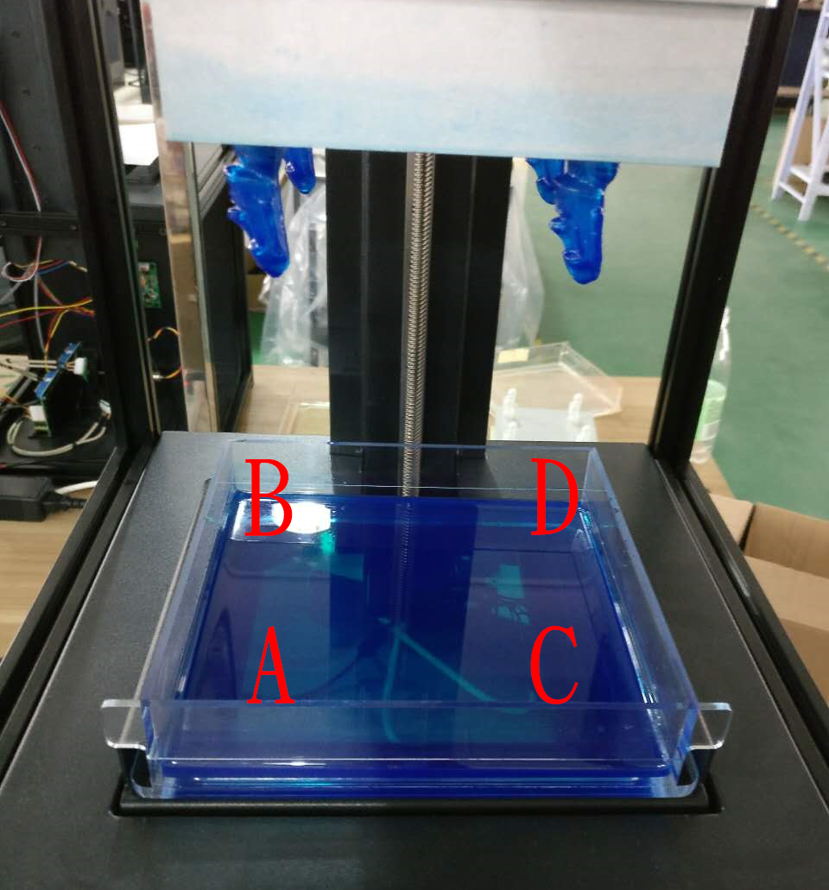
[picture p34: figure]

Couple scenarios can happy:

1. Print is successfully, print sticks to the plate and looks like the ring:

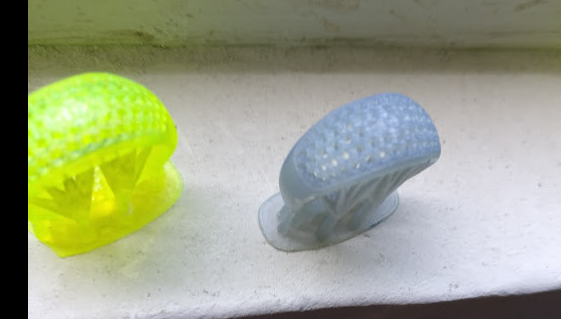
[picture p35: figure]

2. Nothing is on the plate, a flattened piece can be found at the bottom of vat at the B spot
3. A partial ring is printed and seems to broken off from the middle
4. A ring is print it but seemed to have a side of it getting cut off
1. Congrats
2. There are couple possibilities:

Check setting to make sure laser energy is at 61 and xy print speed is at 4

Test print. If it is doesn’t work. Please redo leveling and make sure you follow the steps. If rest position at 188, ½ turn tightening doesn’t work for you, then do leveling at 188 but without any tightening

3. Please increase laser energy to 62 and see if that works
4. Please check to see if any cables blocking laser

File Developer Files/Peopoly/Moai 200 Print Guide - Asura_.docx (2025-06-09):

Intro:

Moai 200 takes Gcode as input for printing. Many steps are similar to FDM printing. However, there are considerations unique to SLA printing and ecosystem. This instruction covers how to print on Moai 200 and how you can build a printing process that suits your need.

While Moai 200 is a SLA printer, it uses standard Gcode as toolpath for its laser the same way FDM printer extruder moves based on Gcode and print layer by layer. Many ideas and considerations are the same. But there are significant difference as well

Same:

- A good first layer. This is as important as FDM. Moai 200 is a bottom up SLA printer, meaning it prints the object upside down. A good adhesion means the object would not break off during the printing or fall down into vat:

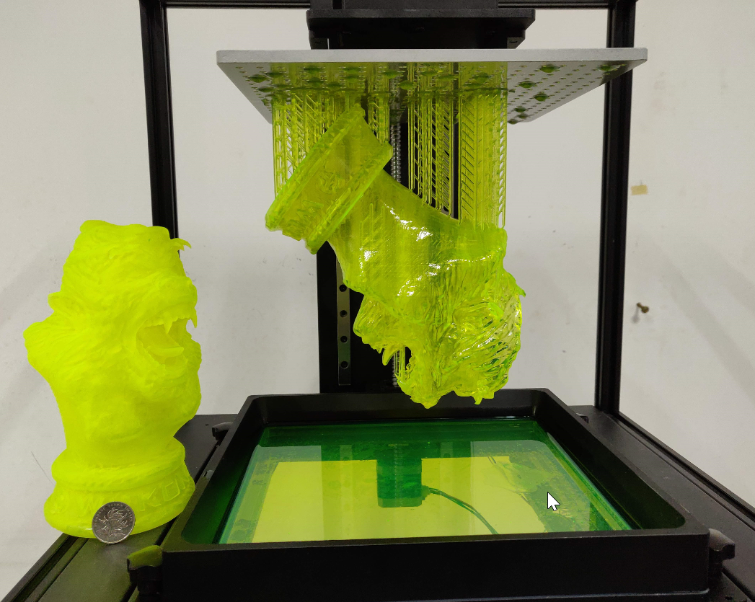
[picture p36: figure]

There are couple ways you can get a strong first layer with longer exposure time, stronger laser power and use of brim. You can also help the object to stay on platform by reducing object weight via hollowing. More on these points later.

- Support generation.

While Moai 200 prints upside-down, it still has to deal with gravity and support is as important as ever. The shape and size of support are different but the idea is the same.

- Speed vs detail.

Like most SLA, Moai 200 typically prints with a layer of 0.025mm to 0.1mm. The more detail, the longer it takes to print. 0.1mm is commonly used for prototyping while 0.05mm is most frequently used. 0.025mm are used for professional results. Anything lower than that can still be done but now the resin’s own error tolerance comes into play. Any desktop level printer talking about printing less than 0.015mm (15 microns) are not be realistic about the materials they used. For Moai 200 printing, we recommend 50 microns and 100 microns for detail, and speed

Difference

- Upside down printing

Because Moai 200 is a bottom up printer like Form1+ and Form2, you have to consider gravity that may pull down the object. This is only a concern when printing large object. The hollowing section deals with this. This also affects how prints are oriented and how you deal with overhang. In general, Moai 200 can deal with overhang very close to 0 degree.

- Resin

Resin is significantly different than filament in many ways. Resin needs post-processing to fully cure it. Resin can also irritate skins so please see the safety section down below. And finally, because the object is immersed in the resin, if the object is hollow, there may be resin trapped inside. When you hollow an object, you should also consider drain holes. These are covered below

Safety

There are two potential safety hazards with laser SLA printers:

- Laser
- Resin
- Post Processing

Laser

Moai 200 uses a 405nm 150mw UV laser. It is considered low powered laser but still can hurt human eyes if aimed directly at the focus length. Therefore, please wear goggle if you are going to be testing it with panels removed. Moai’s panels can block the harmful UV light so you will be ok if it is completely closed. Reflect UV lights are much weaker but still avoid looking at it over extended time.

Resin

Moai 200 Resin, as well as almost all SLA printer resins can irritate skins if it comes in direct contact with the skin. Wear gloves when handling resins and holding not-fully cured objects. Wash with warm water and soap if resin comes in contact with your skin. If your eyes come in contact with resin, quickly wash with warm water only to remove as much as you can and seek professional help immediately. Resin safety has its own safety document in the folder

Post-Processing

High content 90%+ ethanol is recommended for Moai 200 resin. IPA can be used as a substitute. Please wear glove when handling it to avoid directly exposure to skins and eyes or it may cause over-dryness. Please keep it away from flame.

Formlabs has a nice safety instruction that applies to Moai:

https://formlabs.com/support/printers/form-1/safety-first/

Before we gets into the detail, please know that

DO NOT REMOVE RESIN VAT WITHOUT TAKING DOWN THE BUILD PLATFORM.

Forget doing that may result resin on the build platform drip into the system below, causing significant damage to galvo and short the boards.

Print Steps:

This is a set of the common steps in sequence when printing on a SLA printer like Moai. Not all steps are necessary and you may skip 1 and 2 depending on the object. This guide is designed for using Asura to prepare for prints.

This is generally the workflow for preparing a file for printing on Moai

1. Positioning and Orientation of the object.
2. Does object need hollow?
3. Does the object need support and base?
4. Output file for printing (slicing)
1. What is the best position and orientation for the print?

This should be considered with base and support as well. The optimal orientation for an object is to have a high print success rate with least support. This means avoiding having difficult to print sections like islands (parts of the object that have negative angles) or long horizontal feature. At the same, consider having enough surface area to the plate so it can stick well. Let’s use this Peopoly Moai 200 model file as a case study. The file can be found here. (https://drive.google.com/open?id=0Bzke6lBHG_z5Zk1PSnYtVEFKT2s)

When you use load command to open the file, you will find the Moai 200 is sitting in the center of the platform. For most of the models, this may be fine.

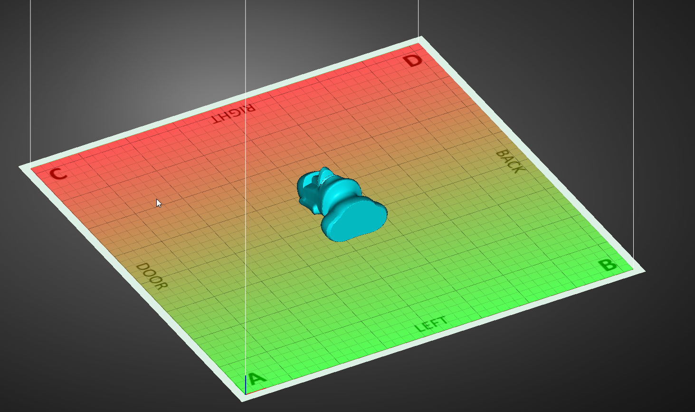
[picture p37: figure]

Here you can see the platform labels out where the model is located in the Moai 200 printer if it is printed as it is. Door is the front door, Left is the left side of the printer and vice versa. As some of you may notice, Left and Right are opposite of what you would expect, and that is why we had to label them.

To move and turn the model, let’s use move / rotate command

You will see the circles of allowing to move and turn the selected model

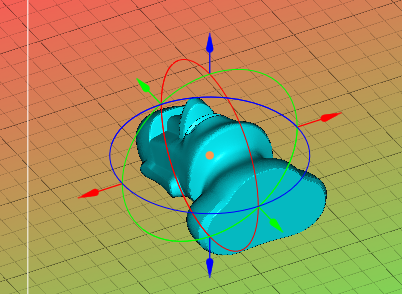
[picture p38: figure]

By clicking and dragging on of the circle, you can turn the model and here is an example.

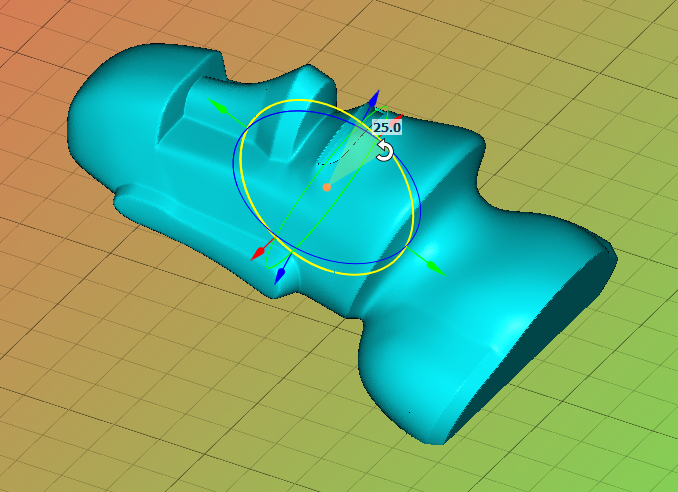
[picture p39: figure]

The number 25 signifies the degree of turning.

Let;’s turn the model by 75 degree, dragging on the red circle

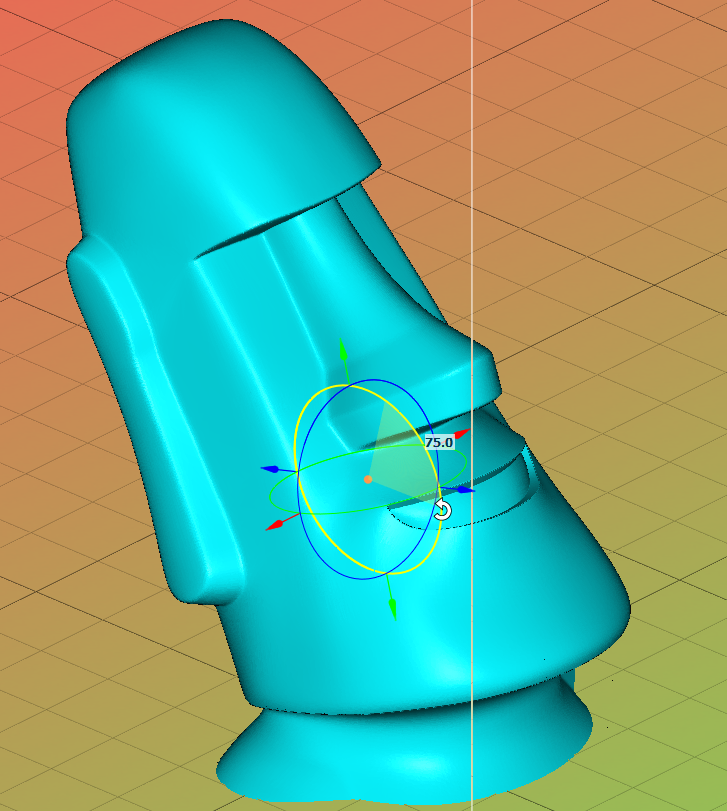
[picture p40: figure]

Click to the platform and you will have

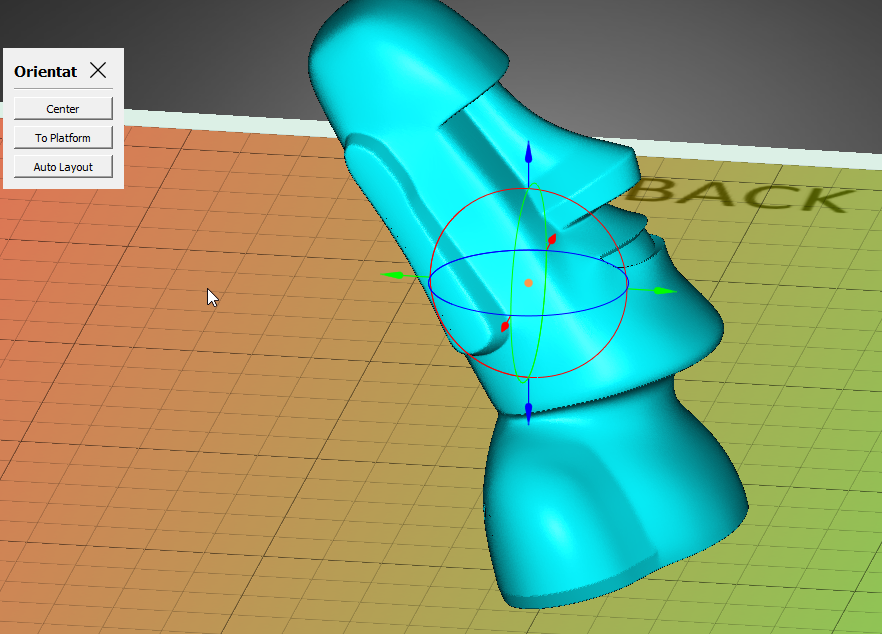
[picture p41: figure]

We select this angle to show minimize the maximum surface area of the layers so that it has the highest print success rate with the least amount of the support.

2. Hollowing

One of the key factors when printing on “Bottom-Up” SLA printer that does not exist on FDM is the weight of the object and the cost of resin. Thus hollow out a model is an important tool for user as it can save a lot of time and resins.

The decision is as such:

Can the object to be too big and too heavy such that it may fall out of the platform and into the vat?

Is transparent resin used? Because it may show the internal support if the object is hollowed out

Save some resin?

How to decide:

If you are printing a solid object with a large internal volume, then it may be best to consider hollowing out.

This is the hollow function in Asura

After clicking it, the model is hollowed out and shown in different colors

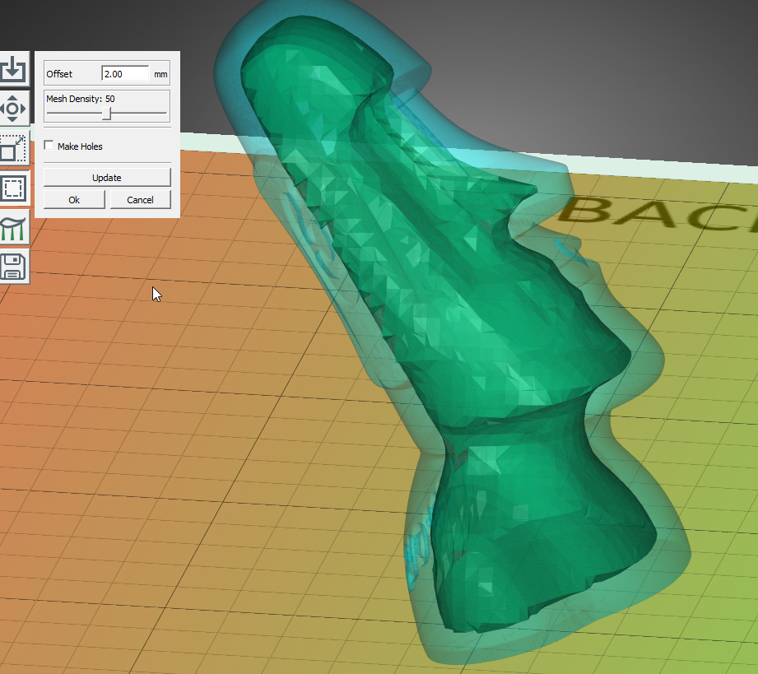
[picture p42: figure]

The lighter bluish green is the solid part while the deeper green within the object is the hollowed out portion.

The offset here means the thickness of the shell. 2mm is a good starting point and you could make it thinner to save resin and time. However, under 1mm is not recommended and the results have a lot to do with the type of resins you are using. Resins with high hardness can print thinner wall while softer may not be able to print thin wall as well.

The mesh density is how accurate the internal hollowed part is and for most of you, just leave it at 50 is fine.

When you hollow a model, you almost always create holes so that resins trapped inside can be drained. And you would need at least 2 holes for drainage to work properly

By clicking Make Holes, you can get additional functions

Here the cursor becomes a guide for drilling holes based on the paramters. We recommend radius to be 1.5mm if you are not sure how to start.

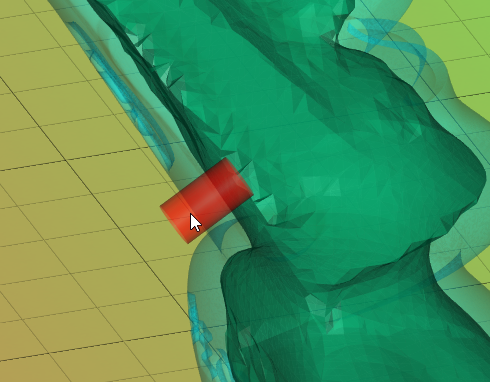
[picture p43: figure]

Here you can left click to pick the spot to tap holes and right click to remove spots that are tagged for new holes.

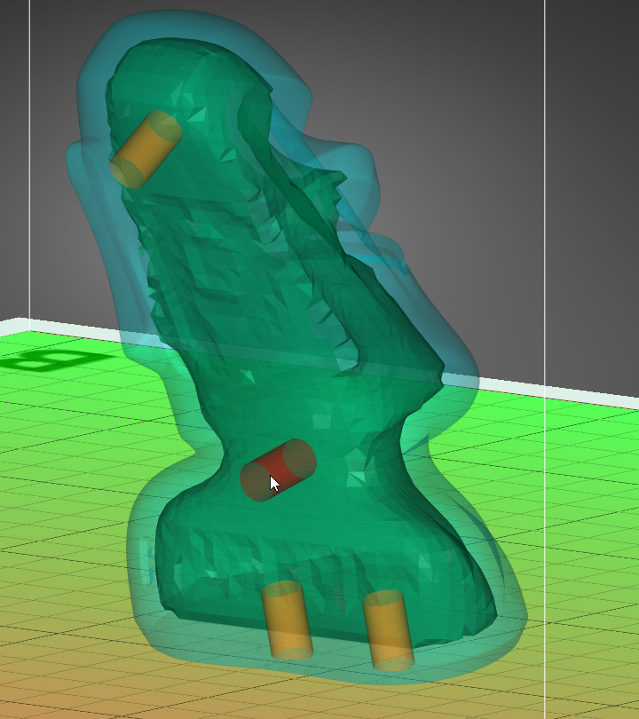
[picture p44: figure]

Click Ok and you have a hollowed and tapped model

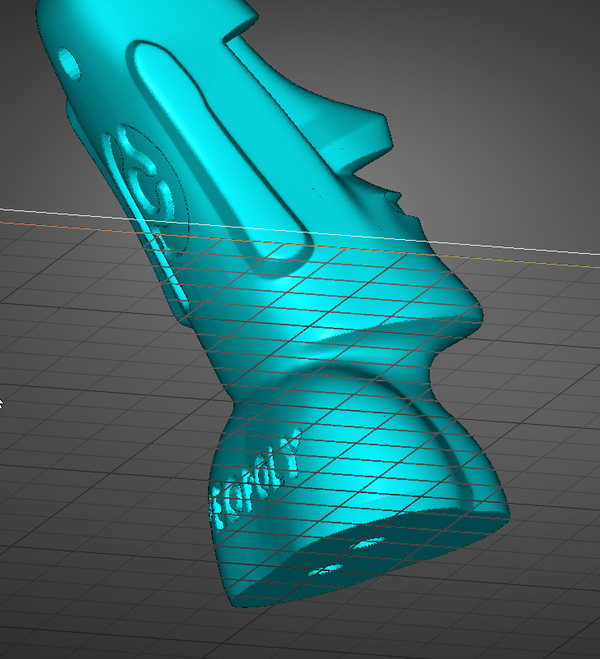
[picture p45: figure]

3. Support generation (v3 Asura)

Support generation is a key part of the printing process. SLA and FDM printers are so different, they require a different type of supports for overhangs. Asura is specifically designed for resin printing and has very user friendly features.

Before we proceed, make sure your support parameters are set as below. You can click on the small triangle on the right of the parameter to open up settings

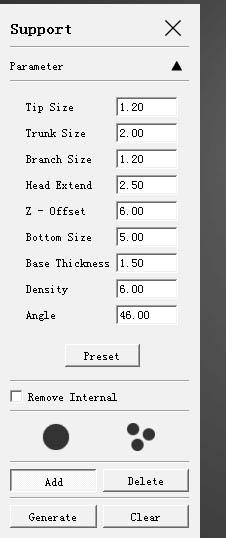
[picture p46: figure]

Make sure the individual base is selected

For most of the users, simply click and select generate and you are ready to move to next step. Or if you want it quickly, right click on the model and select Auto Support. This creates a full base, raise the model up to 5mm clearing from the build plate and add support.

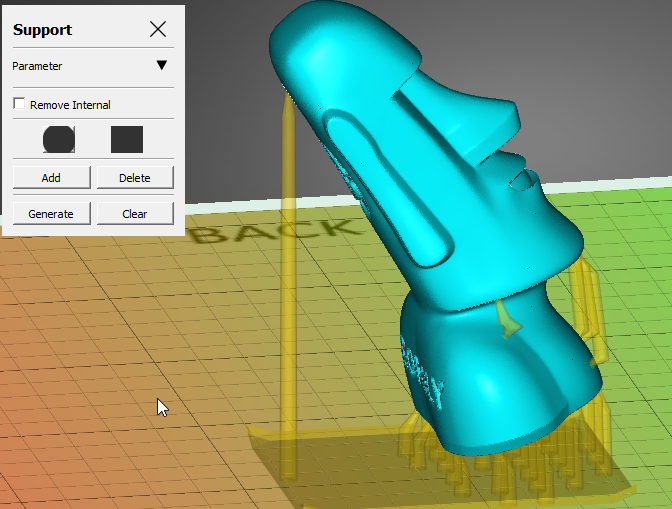
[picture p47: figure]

If you don’t like what you see, you can also click on add / delete to manual edit supports.

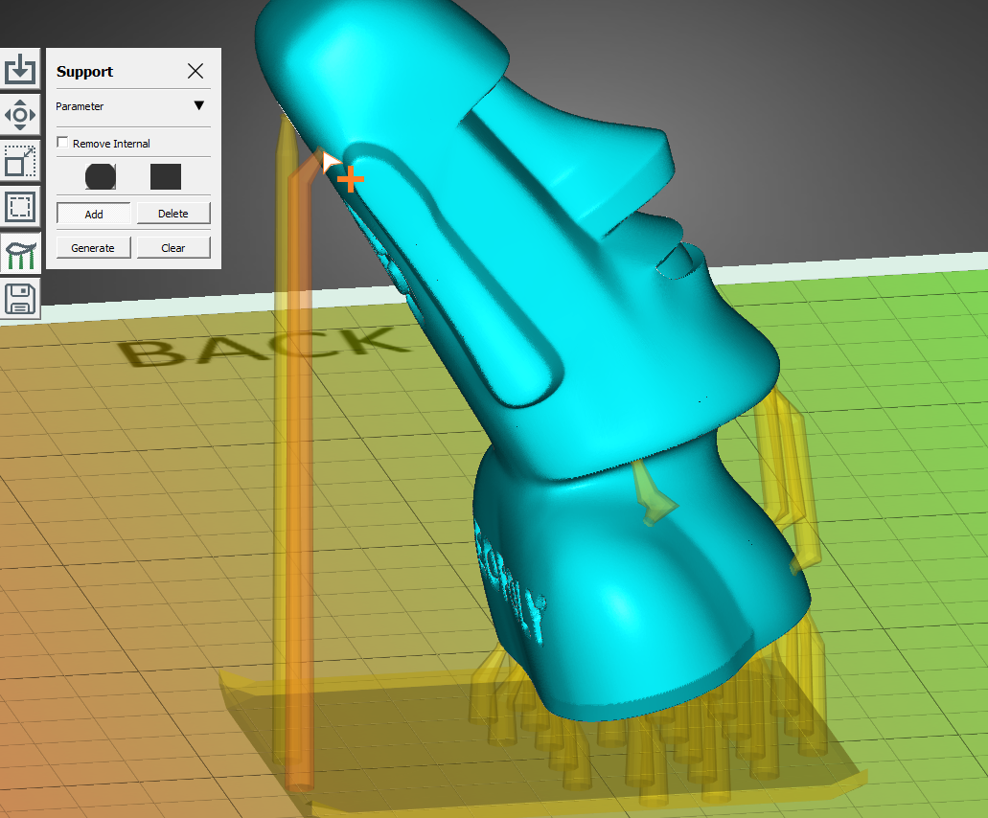
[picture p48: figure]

You can learn about support’s parameters in Asura user guide. (https://docs.google.com/document/d/1ujuHiMBNtAiURRonDJZQ4sKzHopYzQR3W7yzaehJ2Jc/edit?usp=sharing)

Slicing (V3 Asura)

Asura uses Cura software engine to convert model to a format that Moai 200 can print. We have simplified the process in Asura such that all you need to do is

1. Select Export
2. Pick a layer height. 100um is very popular and useful for most applications

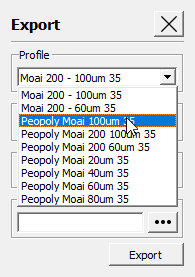
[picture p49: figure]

3. Click to give the file a name (make sure it is no longer than 25 characters)
4. And click to save the gcode

Save the gcode to SD card. Ignore the print time as laser moves much faster than extruder. It is often one sixth or even less time.

And make sure place the gcode in the gcode directory of the SD card (X:\gcode\)

File name should have less than 25 characters

And you are ready to print

The positioning of the print

Below is how print positions on Cura compares to its location when printed in Moai:

A->A and vice versa.

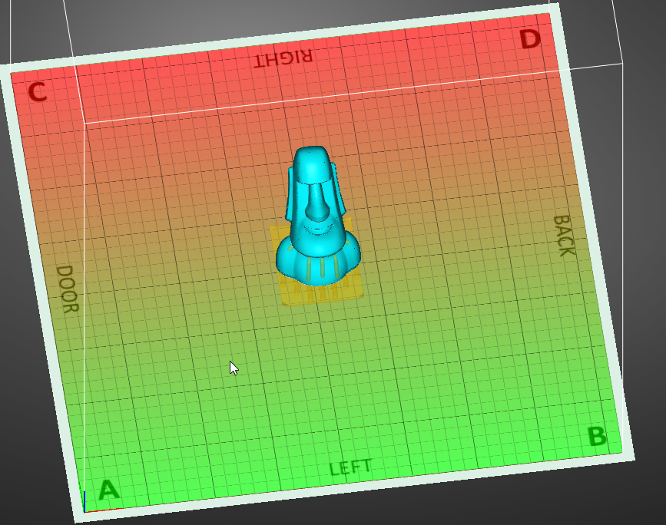
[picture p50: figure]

Extra notes on Gcode:

You could use other slicers but some of the display feature may not show correctly and has unneeded starting gcode.

Basically, Moai 200 interpret only a few gcode command:

G0 G1 for movement. F for speed and E for exposure

Home command works as well. Because there is no filament, there is no need to extrude a little bit before printing, please remove that code if you are using your own slicer

Notes on Exposure

a bit about laser power, exposure and resin as you guys starting to print and experiment:

1. the more transparent and lighter the color, the less energy they absorb, thus needed higher exposure. keeping laser light constant black/blue can go up to 100 while clear may be around 75mm with laser power holding constant

2. higher exposure can be achieved by higher laser power and/or slower laser speed

3. the photosensitive chemical reaction does not correlate linearly with exposure amount. this means you cannot cut the laser energy by simply half and cut the speed down by half and expect the same results. once laser power drops to a certain level, it will not cure fast enough to have a good success rate

4 The best approach I found so far is to find the minimal laser energy that will solidify with a print speed of 80mm/s for layer height at 0.1mm. and then fine tune by increase / decrease speed. the lower laser power you can get away to do successful print, the better surface finish as laser spot would be smaller

Post processing

This is the least fun part of any kind of 3D printing but a necessary step. When Moai 200 or any SLA printer finishes a print, the resin is cured enough to create a solid shape. However, it is still soft and not completely cured to achieve its final physical look and mechanical property. More is needed.

3 key stages of post-processing:

- Removal of the print

Please use metal scraper to chip the print off the built platform. This will feel like printing off FDM. First you have to loose the bolt on top of the build platform. When you remove the platform, please turn it over the platform surface face up quickly so the resin doesn’t drip to your hand or to get on the printer. Because prints are still not fully cured, please be careful not to chip the object with sharp item or it will leave marks. You can first scrape off resin on the platform (not on the object) back to the vat before removing the object. This helps recycle some resins

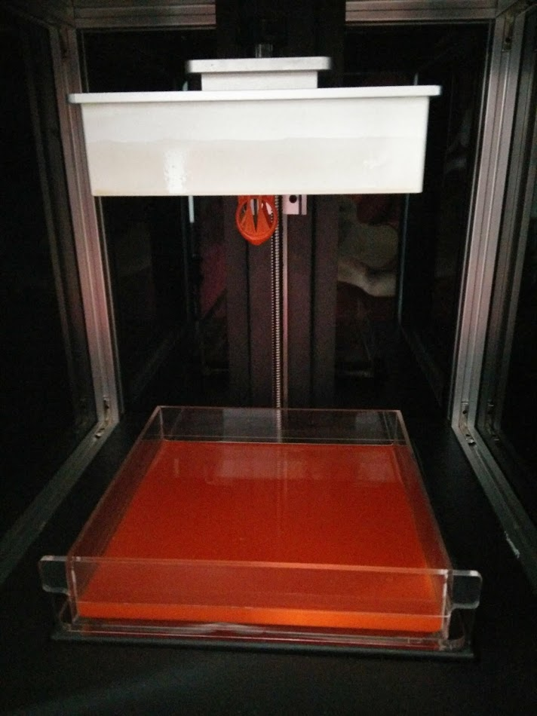
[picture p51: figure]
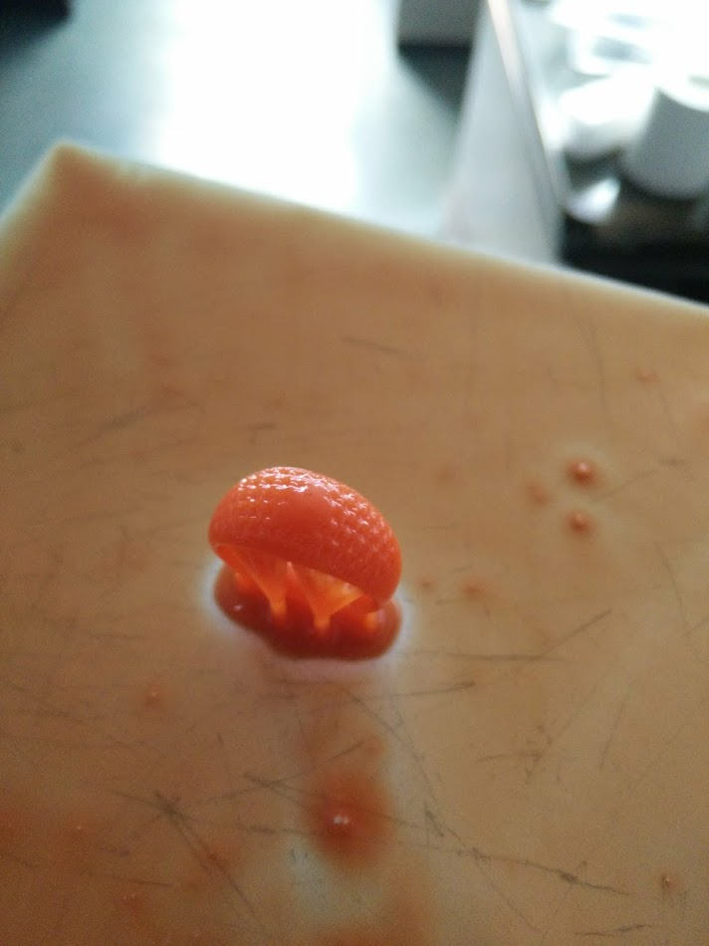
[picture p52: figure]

- Washing off

Not only object is not fully cured, there are resins sticking on the object. We must first removed those resins by use ethanol.

Have 2 containers, one filled with ethanol (not 100% filled, 30%-50% depending on the depth). And one filled with water. Dip the object in ethanol first and quickly shake for 30 seconds before put the object into the water and shake for 10 seconds. Repeat this at least twice. More if there are still resin on the object. There is no need to submerge object in the ehanol for extended time (>2 minutes).

- Final Curing

Please the object under direct sunlight or under UV light fixture. Sunlight is slower but free, and can be speed up by submerge the object in water. UV light is quicker but need special equipment.

Formlabs has a nice guide that applies to Moai:

https://formlabs.com/support/finishing/post-print-steps/

After curing, you could use UV blocker like this: http://www.krylon.com/products/uvresistant-clear-coating/

To prevent further over-curing that may lead to brittleness.

Cleaning

This is definitely the least fun part of the process. You do not need to clean the vat or the system all the time but you may need to, especially after a failed print.

To prevent failed prints (and sometimes successful prints) leaving small half-cured objects in vat that could affect future prints, it is best to inspect when there is a failed print. You can inspect by holding the vat up under artificial lights (not UV light).

DO NOT REMOVE VAT BEFORE REMOVING THe PLATFORM

To remove free floating tiny objects in the vat, you can use a flat head tweezer. If there is too many tiny objects in the vat, you could filter out them using a coffee filter

Here is another good write up from Formlabs that apply to laser SLA printer:

https://formlabs.com/support/printers/form-2/keeping-resin-tank-clean/

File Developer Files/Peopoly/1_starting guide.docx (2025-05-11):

*The new user guide can be found here:*

https://peopoly.dozuki.com/Guide/Step+0+-+Start+Guide/1

Steps:

1. Putting the Moai hardware together

The best guide for putting the kit together is to follow the guide here (https://drive.google.com/open?id=0Bzke6lBHG_z5Uk1RTWE0eVNfRUU):

We recommend not finish the final step of putting on righ Panel and move to calibration. Only close the panel after calibration is done.

Content Checklist: Here (https://drive.google.com/open?id=1B0uXz7hV-ck8P0Gu3KoERtkeMGY4Axt0wk5epfuWcyI)

Helpful files:

Or watch the movie step here (https://www.youtube.com/watch?v=0IkJAOsbeYE)

The layout pics are here (https://drive.google.com/open?id=0Bzke6lBHG_z5cVQyWGp2cWZzTzQ):

The screws are grouped into bags and you can reference the labels on the beams to the photos

2. Check

After putting the kit together, (but before putting the side panels on, it is best to do a check.

Please refer to this document (https://drive.google.com/open?id=1R4ggLXtaHLgEfPj2fK2P_7y7HjT0qA91M-NNgyH7Ak4) for the check steps.

3. Software Installation

After calibration, it is time to set up software.

The instructions is here:

Before you can print, you would need to install:

Cura 2.6 from here (https://drive.google.com/open?id=0Bzke6lBHG_z5cjJPNHdXaFZrWWM)

Cura 2.6 profile: here (https://drive.google.com/open?id=0Bzke6lBHG_z5cjJPNHdXaFZrWWM)

Meshmixer

You do not need to install any hardware driver

For cura 2.6

During installation, no need to install Arduino driver:

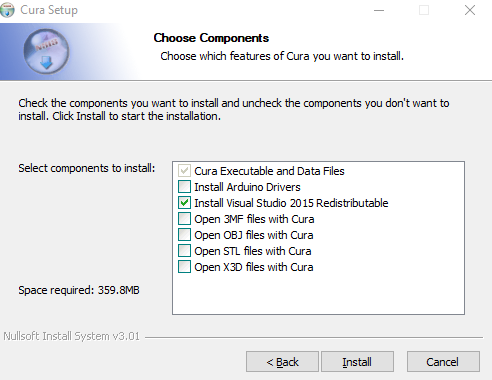
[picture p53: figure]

After the program is installed. Run Cura Moai Edition.

And it will ask you to add a printer.

Please add Peopoly Moai under Other

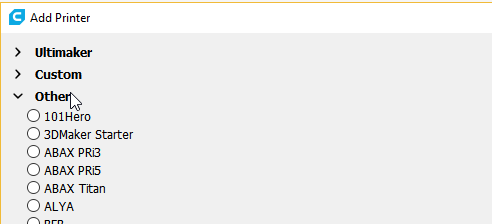
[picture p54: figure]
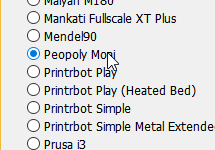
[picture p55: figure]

This will give you correct printer setting

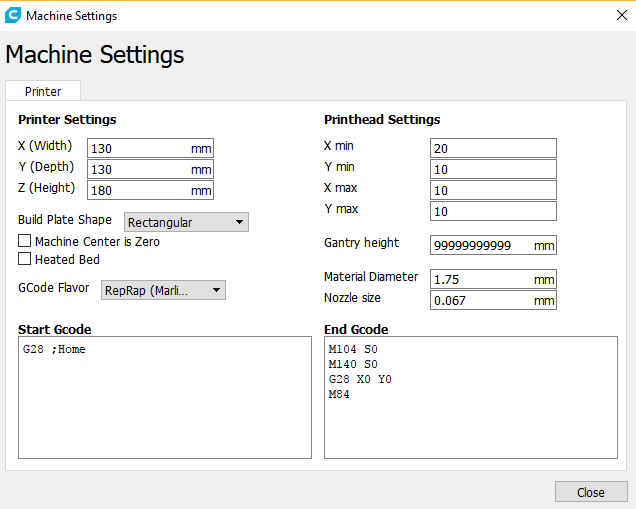
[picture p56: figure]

Next, go to settings -> Profile -> Manage Profiles


Download the profiles from our Google Drive here (https://drive.google.com/open?id=0Bzke6lBHG_z5VG9hTV9KallOTjA)

Extract the files and you will see:

Go back to Cura and Click Import


Import both profiles from files extracted from the downloaded zip file. And you will see:


Make sure all the settings are visible by going into:


Select “Check all”


Now select the newly Imported profile


You are ready to print at layer height 0.1mm

Please select custom for print setup to open up more settings

Quickly check the nozzle size is 0.067mm by looking at line width


And print speed is 85mm/s with first layer 5mm/s for 0.1mm layer height at 61% laser power


Ensure Support is off and Build Plate Adhesion is set to None

4. Dry test (without resin)

Resin can get messy so let’s check functions before we start printing.

You can test print the Moai stl file here (https://drive.google.com/open?id=0Bzke6lBHG_z5NEFJYzdoVlZIU3M) using the settings.

- Load the stl file into Cura
- Move it to C spot indicated below on Cura platform


Like this


- Use Cura to slice the file,


- save to SD card’s gcode directory and
- Put the SD to the printer and print from menu

As it goes to each layer,

Check the peel action at each layer and see if Z-axis is moving correctly. It should steadily move upward.

This is Cura’s platform:


Action sequences should be:

Laser scan the toolpath -> peel action (the VAT is tilted) -> platform moved upward

First layer will be slow because just like FDM, we want good adhesion to platform and we use much longer exposure time to make sure that sticks well. (you can see that in cura settings)

If it goes smoothly with no loud noise or sudden stoppage, we can move to full printing. If something is going wrong, hit the power button and it will reset.

5. Printing instruction

Full printing guide is here (https://drive.google.com/open?id=1wZhVToWbOOYvWisfJB7dk12SeblLANutIcp-jKCTicw)

5.1 Leveling instruction (https://drive.google.com/open?id=1MeXCjGVIVvCN8XrciehLLfmdflCe3DazT6CqE1-7oew)

5. Resin handling! Very important

The above setting is only for the resin we send you. UV Resin from other brands can work but will have different settings. Here are some of the things you need to know about handling resin.

Most UV Resin has very low toxicity. However, it is never good idea to touch it with bare skin and definitely not a good idea to contact eyes or to ingest. If that happens, wash with warm water. If you get some on your hand, it may cause some itchiness. It is very recommended you wear disposable gloves.

Here are some good info from Formlabs:https://formlabs.com/support/materials/resin-care/

https://formlabs.com/support/printers/form-1/safety-first/

Before you pour resin into the vat, make sure you shake the resin bottle well. Do not pour more than half of the vat unless you are printing something big. For testing, fill one-fifth of the tank is more than enough. When you pour, there will be bubbles in the resin, let it sit for awhile before you start printing. Some resin is sensitive to temperature. It is best to print between 20 - 30 celcius.

Once you start the printing process, wait for the layers to build up and observe for formation of layers. It usually takes at least 30 layers to be easily visible. If you hear a suction sound, it means resin is sticking well to both vat and the platform. If suction is super loud and continues after 30 layers, you may consider stop printing to make sure it is not sticking too well. Resin curing too well may damage vat too quickly. This is something quite unique to SLA printing process.

A very critical part of the printing process is that:

NEVER REMOVE VAT when the build platform is still on the printer. This is because there may be resin stick on the platform and may drip down into the printer laser/galvo if you remove the vat first. This is very critical!

Post processing:

Another unique aspect of resin printing is post-processing. You can use 99% alcohol to wash off uncured resin sticking on the object. It is best to keep 2 containers, one with alcohol and one with water. Dip and quickly shake the model in alcohol and wash for 30 sec before moving to water to clean some of the mixture off, then move the model back into the alcohol and clean some more again. Do Not Leave the Model in the alcohol. It will damage the cured resin if leave in too long.

Here are some good instruction from Formlabs: https://formlabs.com/support/finishing/post-print-steps/

Cleaning:

It is best to use paper towels to clean resin. Never use a piece of cloth. Just throw away.

You can also use alcohol to clean resin off table and other surfaces but do not get alcohol into the vat to mix in with resin. You can use alcohol to clean back of the vat.

Tools you will need:

2 containers, one for water and one for alcohol.

1 metal scraper just like the one used for FDM printer.

1 plastic scraper for cleaning the bottom of the vat as metal may damage it

99% alcohol for cleaning resin off. Anything above 90% would do

Paper towels

Flat head Picker for grabbing onto the printed object

Safety information is also presented in the print guide. (https://drive.google.com/open?id=1wZhVToWbOOYvWisfJB7dk12SeblLANutIcp-jKCTicw)

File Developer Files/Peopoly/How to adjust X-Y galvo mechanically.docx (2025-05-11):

*(DO NOT EVER TOUCH THE GAVLO MIRRORS in any situation)

If you are having problem adjust X/Y size via setting menu to your preference, you can adjust X/Y size via method 1:

First - set your setting for X/Y size to default 360 in the menu.

Open the left and right panels on Moai and remove build plate.

Run the circle calibration with no resin, no plate and empty clean vat with printed circle sheet

Use a small slotted screw driver (included in the kit) to adjust this screw on galvo driver board. Be very careful about it as a very small turn will affect the size of X/Y. Make sure to set X / Y Size to 90 in the system setting before you do this.


DO NOT TOUCH TINY MIRRORS IN THE GALVO IN ANY CASE, SEE BELOW:


If you have hard time adjust X/Y position (location on the vat) through the X/Y Deviation in the setting menu, you can try following method:

First, set X/Y deviation to 100 in the setting menu

Open the left and right panels on Moai.

Run the circle calibration with no resin, no plate and empty clean vat with printed circle sheet

Use a small slotted screw driver (included in the kit) to loosen thess screw on galvo fixture. You can then turn the galvos by holding the motor part (where power cable is attached) to set its position while laser is scanning the circle. Be very careful about it as a very small turn will affect the deviation of X/Y greatly. And do not touch the mirror part of the Galov. See below picture:


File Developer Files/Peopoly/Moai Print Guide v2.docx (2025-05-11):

Intro:

*If you are Windows users, we highly recommend you follow Moai Print Guide with Asura. (https://docs.google.com/document/d/1YDDTXiwi00KFVIGMVTl7Ke_9gclbFdYEs6FMxEuQ6XM/edit?usp=sharing)

Moai takes Gcode as input for printing. Many steps are similar to FDM printing. However, there are considerations unique to SLA printing and ecosystem. This instruction covers how to print on Moai and how you can build a printing process that suits your need.

While Moai is a SLA printer, it uses standard Gcode as toolpath for its laser the same way FDM printer extruder moves based on Gcode and print layer by layer. Many ideas and considerations are the same. But there are significant difference as well

Same:

- A good first layer. This is as important as FDM. Moai is a bottom up SLA printer, meaning it prints the object upside down. A good adhesion means the object would not break off during the printing or fall down into vat:


There are couple ways you can get a strong first layer with longer exposure time, stronger laser power and use of brim. You can also help the object to stay on platform by reducing object weight via hollowing. More on these points later.

- Support generation.

While Moai prints upside-down, it still has to deal with gravity and support is as important as ever. The shape and size of support are different but the idea is the same.

- Speed vs detail.

Like most SLA, Moai typically prints with a layer of 0.025mm to 0.1mm. The more detail, the longer it takes to print. 0.1mm is commonly used for prototyping while 0.05mm is most frequently used. 0.025mm are used for professional results. Anything lower than that can still be done but now the resin’s own error tolerance comes into play. Any desktop level printer talking about printing less than 0.015mm (15 microns) are not be realistic about the materials they used. For Moai printing, we recommend 50 microns and 100 microns for detail, and speed

Difference

- Upside down printing

Because Moai is a bottom up printer like Form1+ and Form2, you have to consider gravity that may pull down the object. This is only a concern when printing large object. The hollowing section deals with this. This also affects how prints are oriented and how you deal with overhang. In general, Moai can deal with overhang very close to 0 degree.

- Resin

Resin is significantly different than filament in many ways. Resin needs post-processing to fully cure it. Resin can also irritate skins so please see the safety section down below. And finally, because the object is immersed in the resin, if the object is hollow, there may be resin trapped inside. When you hollow an object, you should also consider drain holes. These are covered below

Safety

There are two potential safety hazards with laser SLA printers:

- Laser
- Resin
- Post Processing

Laser

Moai uses a 405nm 150mw UV laser. It is considered low powered laser but still can hurt human eyes if aimed directly at the focus length. Therefore, please wear goggle if you are going to be testing it with panels removed. Moai’s panels can block the harmful UV light so you will be ok if it is completely closed. Reflect UV lights are much weaker but still avoid looking at it over extended time.

Resin

Moai Resin, as well as almost all SLA printer resins can irritate skins if it comes in direct contact with the skin. Wear gloves when handling resins and holding not-fully cured objects. Wash with warm water and soap if resin comes in contact with your skin. If your eyes come in contact with resin, quickly wash with warm water only to remove as much as you can and seek professional help immediately. Resin safety has its own safety document in the folder

Post-Processing

High content 90%+ ethanol is recommended for Moai resin. IPA can be used as a substitute. Please wear glove when handling it to avoid directly exposure to skins and eyes or it may cause over-dryness. Please keep it away from flame.

Formlabs has a nice safety instruction that applies to Moai:

https://formlabs.com/support/printers/form-1/safety-first/

Before we gets into the detail, please know that

DO NOT REMOVE RESIN VAT WITHOUT TAKING DOWN THE BUILD PLATFORM.

Forget doing that may result resin on the build platform drip into the system below, causing significant damage to galvo and short the boards.

Print Steps:

This is a set of the common steps in sequence when printing on a SLA printer like Moai. Not all steps are necessary and you may skip 1 and 2 depending on the object.

1. Orientation of the object.
2. Does the object need base?
3. Does object need hollow? Yes -> Meshmixer

Key factors: size and shape of the print. Need to think about drain holes. Object shorter than 8 cm (z-axis) usually is not a problem. It depends on the size of the base and support too.

4. Support generation? Yes -> Meshmixer

Key factors: overhangs and orientation. Moai resin has a 45 degree angle threshold

5. Print: Cura 2.6 Moai Edition
1. What is the best orientation for the print?

This should be considered with base and support as well. The optimal orientation for an object is to have a high print success rate with least support. This means avoiding having difficult to print sections like islands (parts of object that have negative angles) or long horizontal feature. At the same, consider to have enough surface area to the plate so it can sticks well. This leads to the topic of base

2. Base

If you are printing an object that doesn’t have a flat surface on all side, it may need a base to improve print success. I almost always print with a base. Please refer to “Base” instruction

https://drive.google.com/open?id=1S3Kru1g6sITmppF0Kl85T9vfNQzKC7nvrIKVAE0Ziys

You need to decide on orientation before adding base

2. Hollowing

One of the key factors when printing on “Bottom-Up” SLA printer that does not exist on FDM is the weight of the object and the cost of resin.

The decision is as such:

Can the object to be too big and too heavy such that it may fall out of the platform and into the vat?

Is transparent resin used? Because it may show the internal support if the object is hollowed out

Save some resin?

How to decide:

If you are printing a solid block of object with little nuances, then it may be best to consider hollowing out. Example:

This object has some finely detailed parts but mostly big solid part. This would be a good candidate for hollowing.


This ring is delicate and has a lot of fine feature. Hollowing is unnecessary here.


The way you hollow is use Meshmixer’s hollowing function.


Full manual can be found here: http://www.mmmanual.com/hollow/

Basically, the offset distance is the wall thickness and you don’t want less than 1mm. And you would want to drill holes (it is part of the function).

Double click the spot where you feel drain hole is needed. It is recommended to have 2 drain holes per hollow section so resin would not be trapped. One drain hole should be at top part of the hollow section and the other on the side, ensure air can enter and resin can escape.


3. Support generation (V2 updated, do not use Print Studio)

Support generation is a key part of printing process. SLA and FDM printers are so different, they require different type of supports for overhangs. There are a lot less software for SLA than for FDM and we recommend 2 good ones we tested. Some models have pre-generated support then don’t create your own support and you can skip this part.

Meshmixer -

Meshmixer a tool for adding support

Before doing any work, first thing is to check for mesh errors.


Auto-repair does it for me 99% of time.

Then depend on the object, you select what to do next.


I go with smooth fill but flat fill works as well and is a little faster.

Base

If object has a pre-built base, that is usually the preferred way to print by the original designer. You don’t have to follow it but it is usually a good idea to do that. Refer to 1. Base section for an easy way to add base


Orientation

If it doesn’t have a base or you want to test to see if there is a better angle, you can use orientation function in analysis


45 degree is what I use. You can go for less overhang if you want to play it safe. This number should match what you will use in the support. However, with bottom up printer, anything with overhang angle over 0 can be printed without support. This will be shown in the next section more. Orientation decision has a lot to do with if there is a base already, and minimize support vs print success

Support Generation

Use Overhang in Analysis.

Make sure it is i SLA/DLP printer mode if this is the first time you are using it.

Angle Thresh is set to 5 (you could set it higher but it may add too much support)

Angle = 0


Angle 45


Y-Offset is how much it will raise the object up from platform. This is a SLA-specific function as first couple layers are affected by silicon in the vat.

This object has a base already so it does not need Y-offset so I set it to 0. As mentioned, I almost always print with base. With y-offset = 3, this is what it looks like:


And you can click generate to get support. Click done and you can export


If you don’t like it, click remove support and change setting.

Then

Export to STL


Some interesting settings to modify if needed:


DON’T Change later height, it is broken.

Tip Diameter is for tip of support, larger means it has a better grip on the object.

Base Diameter is the support beam base, the larger means better grip on the support. I often bump it up to 8mm when I print without base so this will act like a base with a y-offset

Slicing (V2 updated)

We use Cura 2.6 for slicing and optimize it for Moai. It has Moai settings built in and we made custom Moai profiles for it.

The only part you need to adjust for printing in Cura after import presets are the print speed.

The print speed (movement of the extruder) in cura will be translate to the speed of laser spot movement. Essentially, the laser spot will move through the toolpath from slicing the same way a extruder would move in a FDM printer. To reduce exposure, you increase the speed (thus making reduce how long a laser spot stay in one spot) and vice versa for increase exposure.

Here, the standard exposure time (print speed) are in 85mm/s value

There are Travel speeds settings, thus have 300 mm/s value

And the initial layer print speed is 5 mm/s unless there is a good reason, do not change. And don’t change initial layer height either!


Please make sure support is off

And Brim is enabled with 20mm line count

Recommended setting for included resin:

Energy level set to 58% (from advanced setting on printer)

0.1mm Print speed is 85mm/s, first layer is 5 mm/s

0.05mm Print speed is 130mm/s, first layer is also 5mm/s

0.025mm Print speed is 200mm/s, first layer is 5 mm/s

Infill is 70% for most prints. 50% for large prints

The first layer of print is always 0.1mm regardless what layer height you are going with. This ensures strong 1st layer and constant 1st layer print speed


To print different heights, just select from the drop down menu


Click on

Wait for the slicing to be finished:

You can see the drain hole here.


Save the gcode to SD card. Ignore the print time as laser moves much faster than extruder. It is often one sixth or even less time.

And make sure place the gcode in the gcode directory of the SD card (X:\gcode\)

File name should have less than 25 characters

And you are ready to print

Positioning of the print

Below is how print positions on Cura compares to its location when printed in Moai:

A->A and vice versa.


Extra notes on Gcode:

You could use other slicers but some of the display feature may not show correctly and has unneeded starting gcode.

Basically, Moai interpret only a few gcode command:

G0 G1 for movement. F for speed and E for exposure

Home command works as well. Because there is no filament, there is no need to extrude a little bit before printing, please remove that code if you are using your own slicer

Notes on Exposure

a bit about laser power, exposure and resin as you guys starting to print and experiment:

1. the more transparent and lighter the color, the less energy they absorb, thus needed higher exposure. keeping laser light constant black/blue can go up to 100 while clear may be around 75mm with laser power holding constant

2. higher exposure can be achieved by higher laser power and/or slower laser speed

3. the photosensitive chemical reaction does not correlate linearly with exposure amount. this means you cannot cut the laser energy by simply half and cut the speed down by half and expect the same results. once laser power drops to a certain level, it will not cure fast enough to have a good success rate

4 The best approach I found so far is to find the minimal laser energy that will solidify with a print speed of 80mm/s for layer height at 0.1mm. and then fine tune by increase / decrease speed. the lower laser power you can get away to do successful print, the better surface finish as laser spot would be smaller

Post processing

This is the least fun part of any kind of 3D printing but a necessary step. When Moai or any SLA printer finishes a print, the resin is cured enough to create a solid shape. However, it is still soft and not completely cured to achieve its final physical look and mechanical property. More is needed.

3 key stages of post-processing:

- Removal of the print

Please use metal scraper to chip the print off the built platform. This will feel like printing off FDM. First you have to loose the bolt on top of the build platform. When you remove the platform, please turn it over the platform surface face up quickly so the resin doesn’t drip to your hand or to get on the printer. Because prints are still not fully cured, please be careful not to chip the object with sharp item or it will leave marks. You can first scrape off resin on the platform (not on the object) back to the vat before removing the object. This helps recycle some resins


- Washing off

Not only object is not fully cured, there are resins sticking on the object. We must first removed those resins by use ethanol.

Have 2 containers, one filled with ethanol (not 100% filled, 30%-50% depending on the depth). And one filled with water. Dip the object in ethanol first and quickly shake for 30 seconds before put the object into the water and shake for 10 seconds. Repeat this at least twice. More if there are still resin on the object. There is no need to submerge object in the ehanol for extended time (>2 minutes).

- Final Curing

Please the object under direct sunlight or under UV light fixture. Sunlight is slower but free, and can be speed up by submerge the object in water. UV light is quicker but need special equipment.

Formlabs has a nice guide that applies to Moai:

https://formlabs.com/support/finishing/post-print-steps/

After curing, you could use UV blocker like this: http://www.krylon.com/products/uvresistant-clear-coating/

To prevent further over-curing that may lead to brittleness.

Cleaning

This is definitely the least fun part of the process. You do not need to clean the vat or the system all the time but you may need to, especially after a failed print.

To prevent failed prints (and sometimes successful prints) leaving small half-cured objects in vat that could affect future prints, it is best to inspect when there is a failed print. You can inspect by holding the vat up under artificial lights (not UV light).

DO NOT REMOVE VAT BEFORE REMOVING THe PLATFORM

To remove free floating tiny objects in the vat, you can use a flat head tweezer. If there is too many tiny objects in the vat, you could filter out them using a coffee filter

Here is another good write up from Formlabs that apply to laser SLA printer:

https://formlabs.com/support/printers/form-2/keeping-resin-tank-clean/

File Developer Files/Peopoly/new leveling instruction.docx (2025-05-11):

*DRAFT*

Since Peopoly built Moai kit to test print before shipping, the leveling should already be close to optimal. Following steps are to help you check leveling and make small changes if needed. You should run the check again when you change vat

Steps

1.

Download this gcode and placed it in the SD card’s Gcode directory

https://drive.google.com/file/d/1REhwgXPzffKO1UOH15q6oeZvWlj-A3Lv/view

You will find this gcode


2.

Install build plate on Moai and make sure the knob is tightened.


3.

Locate the resin vat package and take out the vat. Make sure do not touch the bottle part of the vat.


4

Take out the resin bottle that looks like this:


Shake well before open it for about 30 seconds and then pour resin into the vat:

The printer setup would look like:


Now insert the SD card to Moai and power it on by pressing the power button


Print the gcode by using the control knob to

1. select print
2. Select gcode directory
3. Select DIYTest.gcode file

This print takes about 20 minutes.

This is gcode contains 4 small cylinders, one at each corner of the built plate labeled ABCD.


The lettering represents their location on the built plate. This helps you identify them when they are removed from the build plate.


The way to use these cylinders is that we want the printed cylinders to have a height of 10.6-10.8mm. The height of the cylinder tells us how much pressure is placed on the PDMS layer.

When the print is finished. They should look like this when build plate is facing up to the ceiling:


Check location by removing and cleaning (using Ethanol or IPA) one at the time and match them to this picture. If they don’t match, make sure you are holding the plate in the right direction.

Once you got all 4 cylinders removed and cleaned from the plate, go ahead and measure their heights and marked them by A, B, C, D.


For example, you may have A 10.4mm B 11.0mm C 10.65mm D 10.0mm

This set of number represents how your Moai is leveled. You can use it to help you get to optimal level (10.6 – 10.8mm) and share with those who are trying to assist you.

To adjust, first find the tools for adjustment. Locate this screwdriver from accessory box.


Then you have to look under the build plate form and find the screws like these.


There are one under each corner under the vat. The amount of adjustment to each nut is based on the difference between current cylinder height. This diagram can help you visualize better.


Using above measurements as example

To adjust A corner, find the nut under A’s corner and turn it.

Since A is off by 10.4 – 10.75 = 0.35mm. half turn tightening is 0.35mm increase in cylinder height. You make 1 half turn, and we can ex

B corner cylinder is 11mm. We can do half turn loosening of the nut to decrease the height by 0.35mm. Turning it to 10.65mm

C corner cylinder doesn’t need any adjustment

D corner is 10-10.7 = - 0.7mm. We can do a full turn of tightening of the nut to increase the height of cylinder to 10.7mm.

After adjustment, print the 4 cylinder gcode again, measure and adjust. Repeat this process until you have all 4 corners to be between 10.6 to 10.8mm

Thoughts for improvement.

Adjust cylinder design so that optimal printed height is 10mm. This is easier for the user to calculate.

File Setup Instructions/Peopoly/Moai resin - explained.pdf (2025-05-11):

Share; 0 comments

When we started developing Moai, we knew some of our future users would be first time SLA printer users. Thus, we wanted a resin that gives good resolution and is easy to print and clean. We also know many of our users are model makers and love to sand and paint, so we want a resin that has a smooth finished surface for postprocessing. Here are the details for Moai resin that could help you understand and get better results:

### Overview:

Moai standard resin is a UV curable acrylate-based resin developed for laser SLA printer. It responds to 405nm UV light and has a follow mechanical property:

Hardness (Shore D): ASTM D2240 82
Tensile strength at break (Mpa): ASTM D638M 60
Elongation at break(%): ASTM D638M 8% Young's modulus (MPa): ASTM D638M 830

At 25C degrees, the viscosity is 600cps. Density is 1.13

The ideal printing temperature is 20 to 30C. The higher the temperature, the lower the viscosity and requires less UV energy to cure.

Shrinkage post cure is 6.5% and is consistent for acrylate-based resin

### Exposure:

In the user guide, we recommend laser energy at 61 with default Cura profile. This is selected to ensure high print success rate for new users. Use can dial laser down to increase PDMS lifespan. Using the default Cura profile, the user can print using laser energy between 57-61 for Moai. 57-58 are preferred by experienced users who have been using Moai for production. However, if you find large print not sticking well at a lower energy level, it is best to increase to a higher level. We also have users reported using laser energy at 55/56 but with slower print speed in Cura. Moai is designed for experiments and customizations so find the best settings for your application.

an example of lower laser energy can be found here (https://forum.peopoly.net/t/lower-energy-test-for-moai-resin/637)

Lower energy leads to lower shrinkage during printing and smaller laser spot size.

### Colors and dierence

1

Moai resin comes in 6 colors, and while they are very similar chemically, there are subtle differences besides appearances. In general, the darker the color, the higher the resolution and requires more energy to cure. The difference is small but is observable. For clear and green resin, they overcure more than other colors at 61 and thus may lead to shorter PDMS lifespan than other colors. Black and Gray has the best resolutions and requires slightly more energy to cure.

### Cleaning

The best cleaning agent accessible to most users is Ethanol, follow by IPA. IPA is more toxic and is more corrosive but may be easier to obtain in some countries. Any cleaning agent that is designed to remove oil substances should work but may take more time.

Cleaning instruction with 95% Ethanol is to submerge the print completely and move back and forth for 30 seconds to 60 seconds depending on how complex is the print. Make sure Ethanol can reach every part of the print. In some instances, you may have to remove some support to help Ethanol reach covered part of the print. For very delicate print, you spray Ethanol on the object and let it cleans and drips down. When the dripping no longer contains resin, you can stop. You can use a hair based brush to assist in removing excessive uncured resin from the object.

1



Some user prefers Ultrasonic cleaner with cleaning detergents. This can be helpful but be careful not to overdo it. Ultrasonic can disrupt delicate features and damage very thin walls. Ultrasonic also heats up, and it is NOT recommended to use it in conjunction with Ethanol or IPA.

### Post-Curing

405nm UV light is preferred, but 395nm UV light can be used as well. You can use sunlight if you don't have UV light available. Submerge object in water will speed up the curing process as water blocks out oxygen from interfering with the curing process. When you can no longer easily scratch the print with a finger nail, it is cured.

Share

1

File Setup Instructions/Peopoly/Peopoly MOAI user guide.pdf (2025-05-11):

# peopoly

# Step 0 - Start Guide

This guide help go through steps of building your Moai, testing and setting up printing.

## Written By: Shu Peng

Step 0 - Start Guide | Guide ID: 1 - Draft: 2019-07-22


This document was generated on 2021-12-25 01:30:50 PM (MST).

© 2021 | peopoly.dozuki.com/ | Page 1 of 7

### INTRODUCTION

Thank you for join Moai user community. We hope this guide will help you build your Moai and help you learn about SLA printing

### TOOLS:

Protection Glasses (1)
UV Protection

### PARTS:

Moai SLA Printer Kit (1)

Step 1 — Check Shipping Damage
- This is your Moai kit. Please check for any shipping damage

Sometimes the delivery person may place the box in the wrong orientation. Please make sure the box's longest side is sitting on the floor with the shipping label facing up.

Step 2 — Check Content


- Please use this list (https://drive.google.com/open?id=1B0uXz7hV-ck8P0Gu3KoERtkeMGY4Axt0wk5epfuWcyI) to check your contents


- Be Careful pulling the Galvos out. DO NOT TOUCH the mirrors in any way.
- Use the pictures here as reference
- Use this video as reference (https://www.youtube.com/watch?v=9KpSDj7P90o)

Step 3 — Hardware Installation
- Please use this guide for Moai hardware installation (https://drive.google.com/open?id=1yzSxYxJ2hDWH5Tks4eD-P5XpEBOaRhRxpic4mbyX3ks)
- This is the most time consuming part of the guide. Please allow 4-5 hours for this step.
- You can watch this build video (https://www.youtube.com/watch?v=G5vjkL5vtcQ&list=PLKlntVS2tLE6wdPa8F2uq2FP1hl_ghBCJ) by Chris Russell to go with the manual.
Step 4 — Hardware Testing and Calibration


- Please Follow this guide (https://drive.google.com/open?id=1R4ggLXtaHLgEfPj2fK2P_7y7HjT0qA91M-NNgyH7Ak4)

Step 5

Do not overfill the resin tank or you will have a mess dripping all over your electronics. When the build plate drops the resin level rises significantly.

Step 6 — Check for latest settings

As the community gains more experience using Moai, we will develop even better printer settings and profiles. Please visit our forum link below for the latest systems, profiles and software:

- Latest settings, profiles and software (https://forum.peopoly.net/t/latest-settings-profiles-and-documents/234)

Step 7 — Software Installation
- Follow steps here (https://drive.google.com/open?id=17nKJrZDkb8WA0aMEBN1xEAxEslRPMuqWTw_dSSEVjws)
Step 8 — How to Print
- Here is the print guide (https://drive.google.com/open?id=1wZhVToWbOOYvWisfJB7dk12SeblLANutIcp-jKCTicw)

This guide is the starting point for Moai users. It will refer to all the relevant steps and guides to help you start using Moai. The build time is about 4-5 hours for first time builder with some DIY experience. No soldering is needed.

Step 9 — Resin Handling
- Insert wisdom here.

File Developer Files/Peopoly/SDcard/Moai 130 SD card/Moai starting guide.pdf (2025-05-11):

SD card content list:

Moai Startup Guide.pdf (this file)

In gcode directory

PM_ring-test.gcode (ring test gcode file)

4-moai-test.gcode (4 Peopoly Moai test gcode)

P_yuan-test.gcode (Circle test gcode)

DIY-Test.gcode (Check leveling)

DIY-Test2.gcode (Check leveling)

cross-center.gcode (Check center of laser scanning)

In stl directory

ring-test.stl (ring test STL file, in stl directory)

peopoly moai.stl (Peopoly STL file)

In PDF directory

calibration-circle.pdf (galvo circle test for PDMS vat) calibration-circle.pdf (galvo circle test for FEP vat)

In Software directory

Asura-Beta.zip (Peopoly Asura software for adding support 32/64 bit)

Ultimaker Cura-3.5.1-win64.exe (Cura Windows 64 bit Moai version)

Ultimaker Cura-3.5.1-OSX-Darwin.dmg (Cura OSX Moai)

Cura-3.5.1-linux.AppImage (Cura Linux version)

Cura3.5.1 profiles.zip (Cura profiles for 3.5.1)

SD_CardFormatter0500SetupEN.exe (SD card formatter, Windows)

Autodesk_Meshmixer_v3p4_Win64 (Meshmixer Windows 64 bit)

XYZware_Nobel_1.1.30.13.exe (XYZWare for Noble 32/64 bit for Windows)

Please join Moai community to get support and join discussion:

Official Wiki, first place to search for answer

https://wiki.peopoly.net

Official discussion forum:

https://forum.peopoly.net

Peopoly Moai FaceBook group:

https://www.facebook.com/groups/166212290569846/

Guides

*If you have FEP vat version of Moai, there is special instruction for you in the leveling guide, please make note of that.

Main user Guide (Start here):
https://peopoly.dozuki.com/Guide/Step+0+-+Start+Guide/1

Official Wiki

https://wiki.peopoly.net

Hardware Installation Manual: https://drive.google.com/open?id=1yzSxYxJ2hDWH5Tks4eD-P5XpEBOaRhRxpic4mbyX3ks Calibration
https://drive.google.com/open?id=1R4ggLXtaHLgEfPj2fK2P_7y7HjT0qA91M-NNgyH7Ak4 firmware upgrade manual
https://peopoly.dozuki.com/Guide/Moai+-+Firmware+Upgrade/3
Print walkthrough:
https://peopoly.net/blogs/news/moai-work-flow-print-orientation Printing with FEP film:
http://wiki.peopoly.net/doku.php?id=moai:fep
how to add support for printing: https://www.youtube.com/watch?v=AZNsDMUgqWE how to hollow object for printing: https://www.youtube.com/watch?v=ZXu6VYj4Um0 How to restore Vat PDMS Coating https://forum.peopoly.net/t/how-to-restore-your-vat/195
Reference:
Resin Settings
https://drive.google.com/open?id=1t8bjlfk7irSJFy3kzOr-I6SN5acE8UIlOl2E4r3dG_8 Community:
FaceBook group:
https://www.facebook.com/groups/166212290569846/
Official discussion forum:
https://forum.peopoly.net
Moai printables add-on
https://www.thingiverse.com/groups/peopoly-moai/things Application:
Jewlery
https://forum.peopoly.net/t/show-us-your-bits/122

Trouble Shooting:
FAQ:
https://peopoly.net/apps/help-center Support section:
https://peopoly.net/pages/support
Test ring Gcode for checking printer https://drive.google.com/open?id=0Bzke6lBHG_z5ajN6VU1scll6QTQ
Z-axis check to see if arm is wobbling https://forum.peopoly.net/t/check-your-z-axis-screws-for-build-plate-arm/214 Cura fix for OSX user
https://forum.peopoly.net/t/solved-how-to-fix-lf-crlf-in-cura-mac-osx/362 Assembly Holes not tapped: https://forum.peopoly.net/t/assembly-screw-holes-not-tapped/154/14 SD card issue, use SD card formatter: https://www.sdcard.org/downloads/formatter_4/

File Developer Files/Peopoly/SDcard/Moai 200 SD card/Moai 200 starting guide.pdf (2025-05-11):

*please check for extra FEP film in the cardboard inside of the box

SD card content list:

Moai Startup Guide.pdf (this file)

In gcode directory

200_ring-test.gcode (ring test gcode file)

200-4-moai.gcode (4 Peopoly Moai test gcode)

200-yuan-test.gcode (Circle test gcode)

200-leveling-pegs.gcode (Check leveling)

200-cross-center.gcode (Check center of laser scanning)

In stl directory

ring-test.stl (ring test STL file, in stl directory)

peopoly moai.stl (Peopoly STL file)

levelingpeg.zip (leveling pegs)

In PDF directory

calibration-circle.pdf (galvo circle test)

In Software directory

Asura-2.21.zip (Peopoly Asura software for adding support 32/64 bit)

Ultimaker Cura-3.5.1-win64.exe (Cura Windows 64 bit Moai version)

Ultimaker Cura-3.5.1-OSX-Darwin.dmg (Cura OSX Moai)

Cura-3.5.1-linux.AppImage (Cura Linux version)

Cura3.5.1 profiles.zip (Cura profiles for 3.5.1)

SDCardFormatterv5_WinEN.zip (SD card formatter, Windows)

Please join Moai community to get support and join discussion:

Official Wiki, first place to search for answer

https://wiki.peopoly.net

Official discussion forum:

https://forum.peopoly.net

Peopoly Moai FaceBook group:

https://www.facebook.com/groups/166212290569846/

Guides

Moai 200 Main user Guide (Start here): http://wiki.peopoly.net/doku.php?id=moai200:start

Reference:
Resin Settings
https://drive.google.com/open?id=1t8bjlfk7irSJFy3kzOr-I6SN5acE8UIlOl2E4r3dG_8

Application:
Jewlery
https://forum.peopoly.net/t/show-us-your-bits/122

Trouble Shooting:
FAQ:
https://peopoly.net/apps/help-center Support section:
https://peopoly.net/pages/support
Z-axis check to see if arm is wobbling https://forum.peopoly.net/t/check-your-z-axis-screws-for-build-plate-arm/214 Cura fix for OSX user
https://forum.peopoly.net/t/solved-how-to-fix-lf-crlf-in-cura-mac-osx/362 Assembly Holes not tapped: https://forum.peopoly.net/t/assembly-screw-holes-not-tapped/154/14 SD card issue, use SD card formatter: https://www.sdcard.org/downloads/formatter_4/

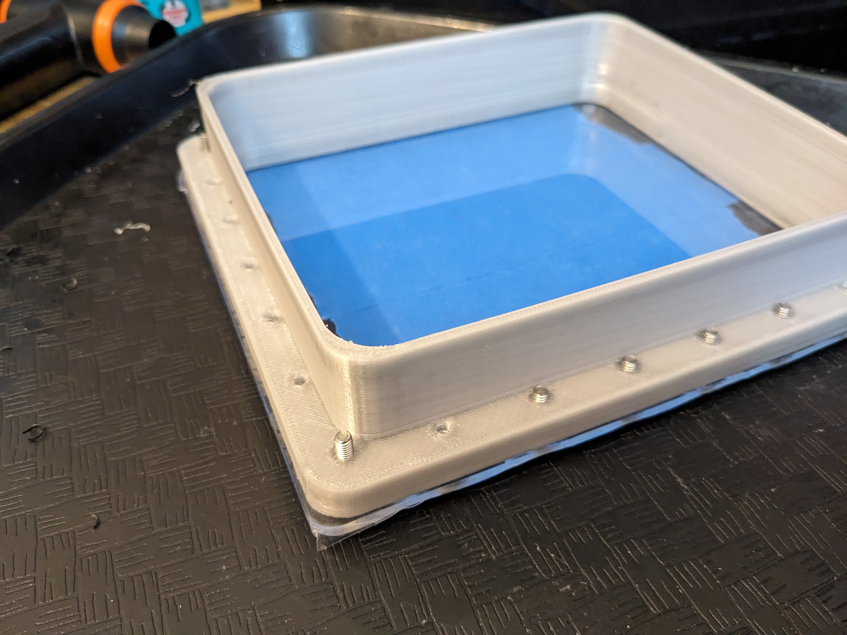
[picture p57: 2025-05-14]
Moai Vats/Printable FEP Vat with acrylic plate/Photos/Assembled VAT using 20mm corner screws 12mm side screws.jpg

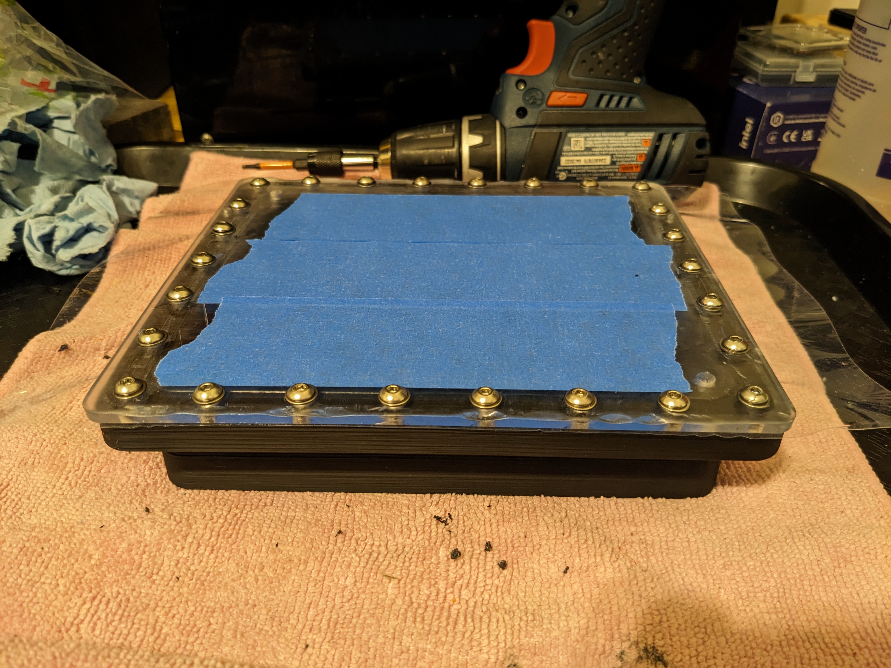
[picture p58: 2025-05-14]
Moai Vats/Printable FEP Vat with acrylic plate/Photos/Plate Ring FEP mounted.jpg

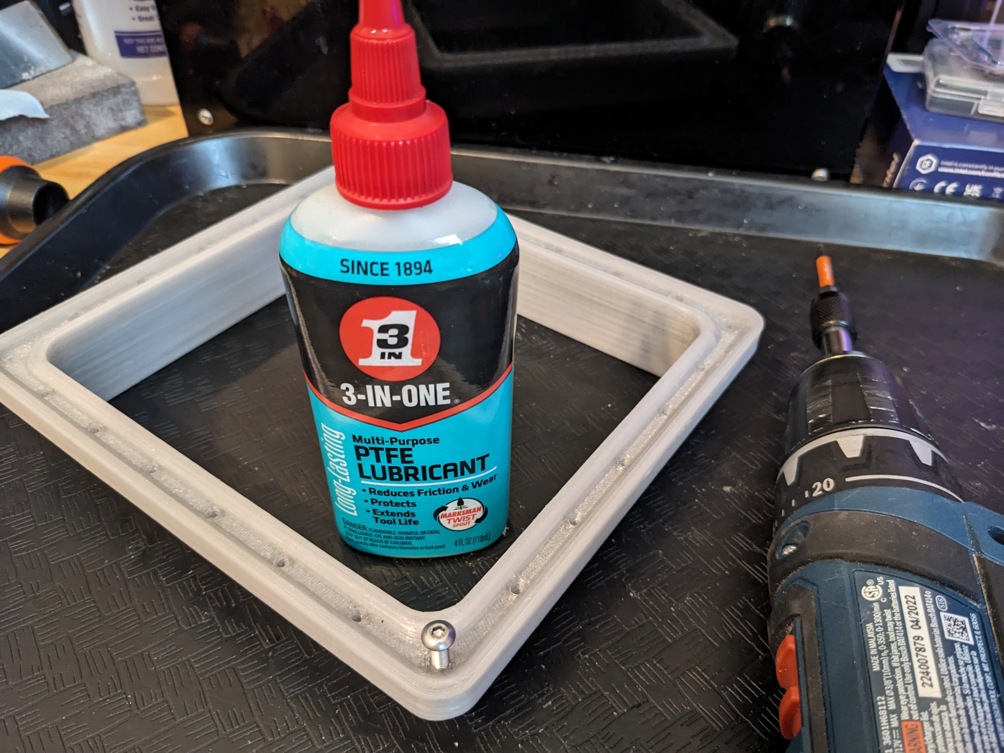
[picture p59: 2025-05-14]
Moai Vats/Printable FEP Vat with acrylic plate/Photos/Preparing threads with oil and screw.jpg

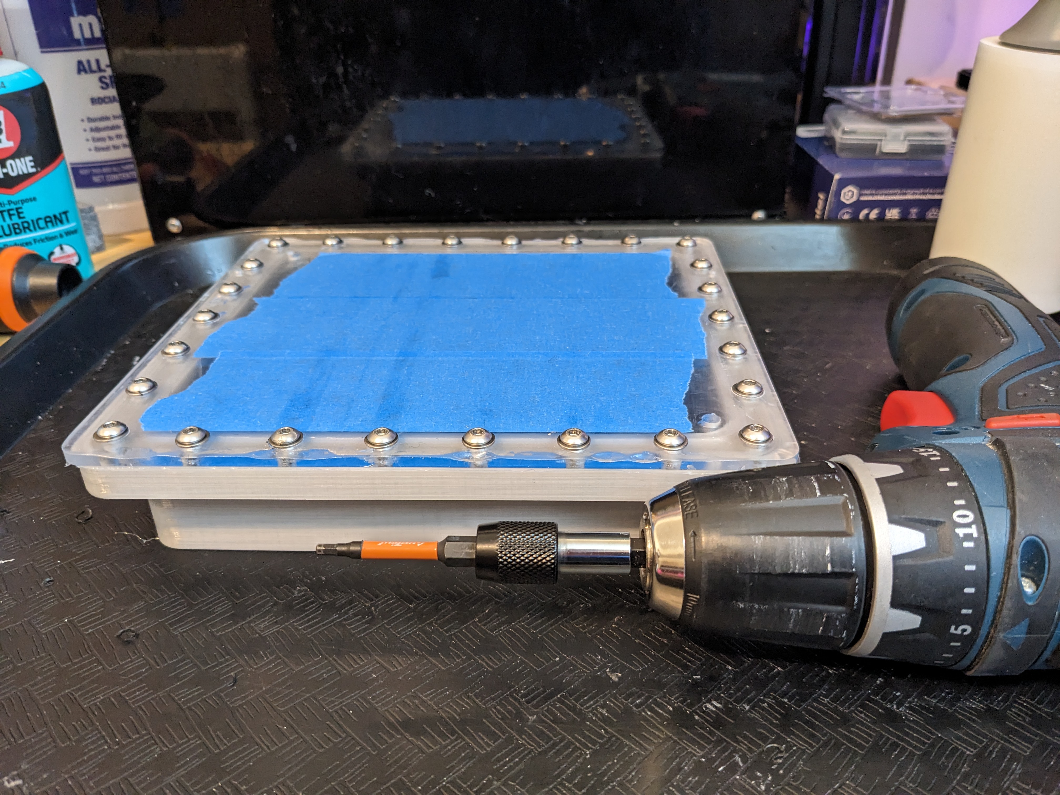
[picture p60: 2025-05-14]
Moai Vats/Printable FEP Vat with acrylic plate/Photos/A torque-limiting driver for scews.jpg

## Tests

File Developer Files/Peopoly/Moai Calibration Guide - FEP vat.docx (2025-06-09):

*draft mode* not ready

Moai Calibration Check

The purpose of this guide is to verify if hardware is installed correctly and set up for printing. This guide does not deal with dimension accuracy and that is covered in a separate guide.

*Please make sure Moai is placed on a sturdy and level surface before begin working.

**FEP Vat users, most of the information still applies to you. If there is a special instruction needed for you, it will be in this green font.

These are the check steps in the order which you will do:

1. Power On
2. Setting Check
3. Galvo Scanning Test
4. Leveling
5. Test Print

Please do not pour resin into vat until the instruction tell you so or it will make testing more difficult.

Moai is shipped with galvos and plate calibrated to work together. To make sure everything is still working after delivery, we will run three tests:

1. Power on Check

DO NOT INSTALL BUILD PLATE OR PUT ANY RESIN INTO VAT for calibration test

Click the Power Switch on the Front Panel to Turn on the Machine (pic)

Two things to look for here:
- The Z Axis will raise to the top and stop at the end stop sensor
- The Vat holder will run to the top of the travel (the clicking sound is normal) and then perform a tilt action and then return to the level position


You should see this screen when Moai is ready:

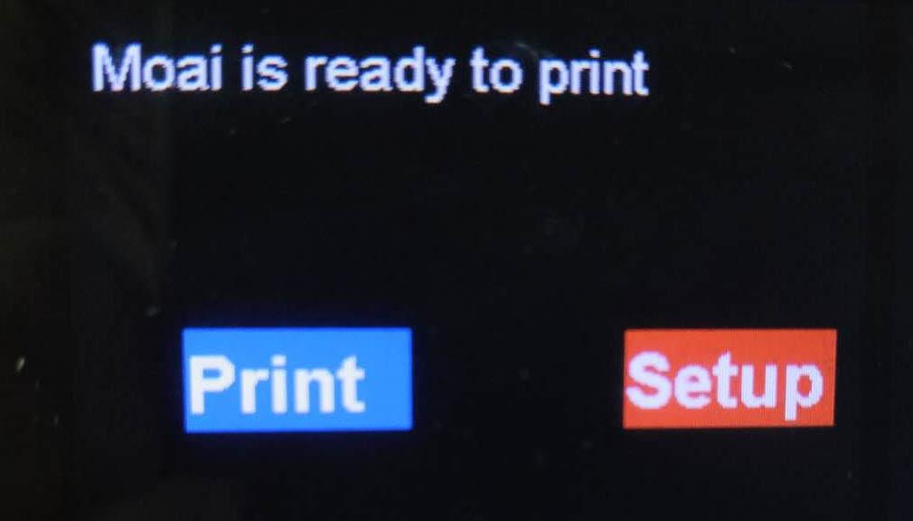
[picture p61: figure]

2. Setting check

Use the Control Knob above the Power Switch to move between “Print” and “Setup”

Press the knob to enter “Setup” (Double press to go back)

Please check your setting and adjust to match the picture below:

If the settings do not match, you can select and click on each entry to adjust the value to match the default values.

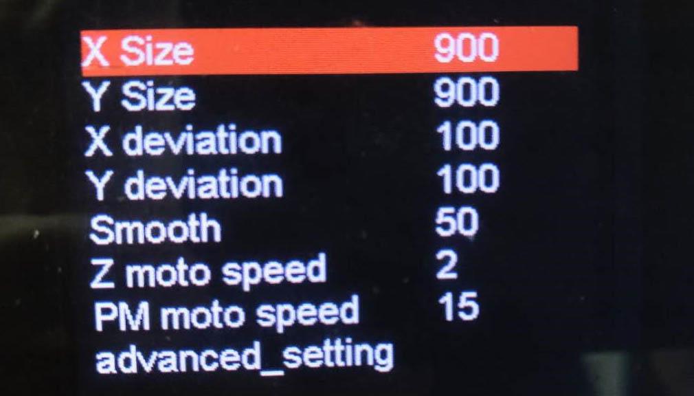
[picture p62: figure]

Then use the Control Knob to scroll down to advanced_setting and click to the next screen. Check to see if the settings match this screen also.


Laser power is a key setting. We like to set it around 57-58 for Peopoly standard resin. Please check against that. Non-Peopoly resin may need to have a lower or higher laser power.

*For FEP Vat users. The Z Reset Position should be 1816

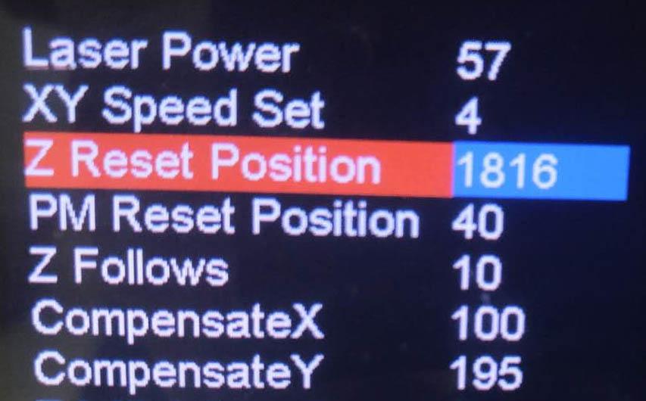
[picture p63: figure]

3. Galvo test

Please download following files

calibration-circle.pdf: https://drive.google.com/open?id=0Bzke6lBHG_z5MkhwQjZ0bk5UaXM

(This file is also located in your SD card’s pdf directory)

https://drive.google.com/open?id=0Bzke6lBHG_z5NmdFUmZENDZ0OEk

(This file is also located in your SD card’s gcode directory)

Print the calibration-circle.pdf and cut it to the outer square and place it in the Vat.

Insert the vat with the printed calibration-circle into the Moai.

NOTE: Make sure the Calibration Circle PDF is printed at 100% scale, do not use the Fit to page option. The dimensions of the printed box should be 5-1/8" (130.18mm), and the largest circle should be 120mm diameter.

Note how the inside squares and circles are shifted. The side with the narrow spacing should be to the back of the Moai nearest to z-axis linear rail when the vat is installed.

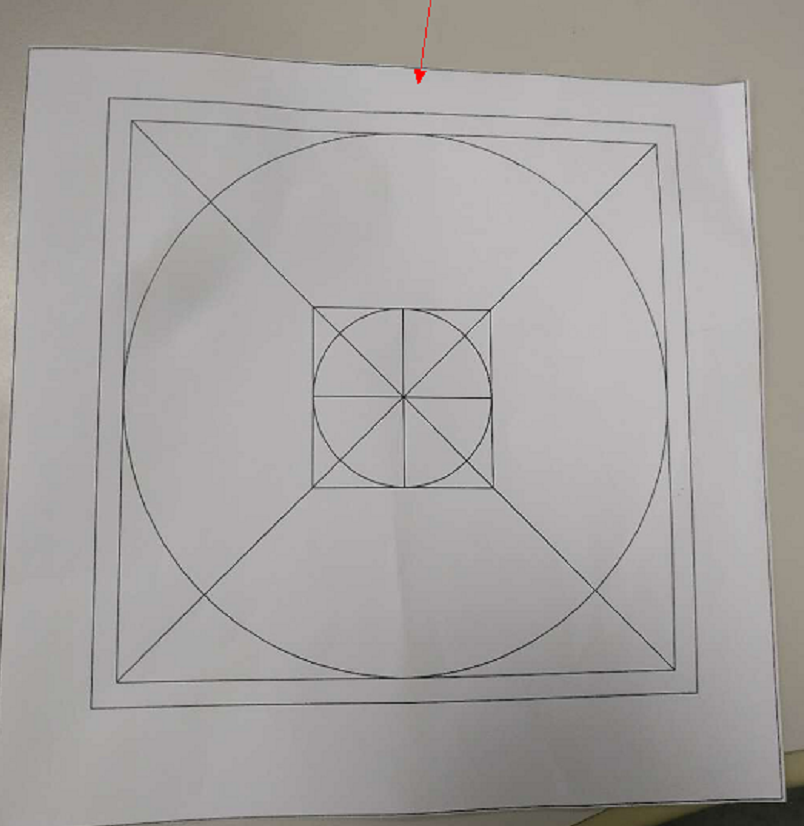
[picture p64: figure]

* For FEP vat users, use a specially made calibration file call calibration-circle FEP.pdf

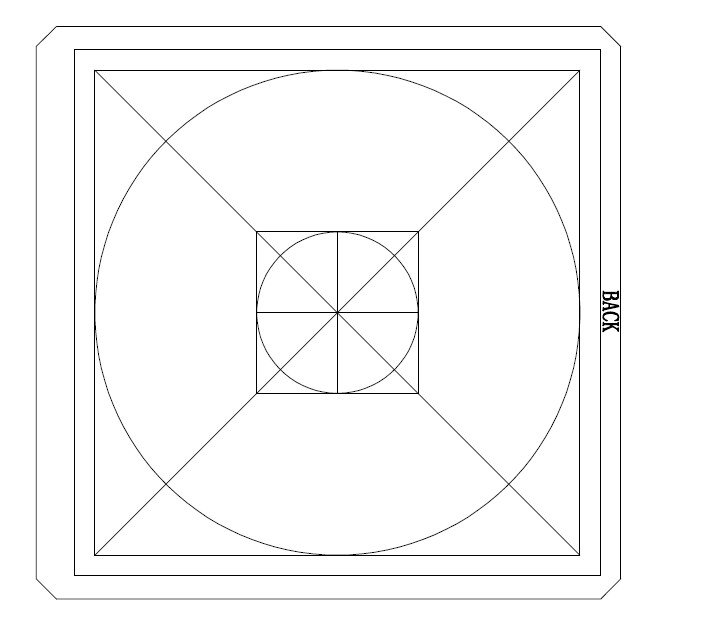
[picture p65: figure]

Circle test Gcode:

Extract P_yuan-test.gcode from P_yuan-test.zip and place the GCode file in directory called “gcode” in a SD card.

Insert the included SD Card in the Machine (make sure you insert with the back of SD card facing up):

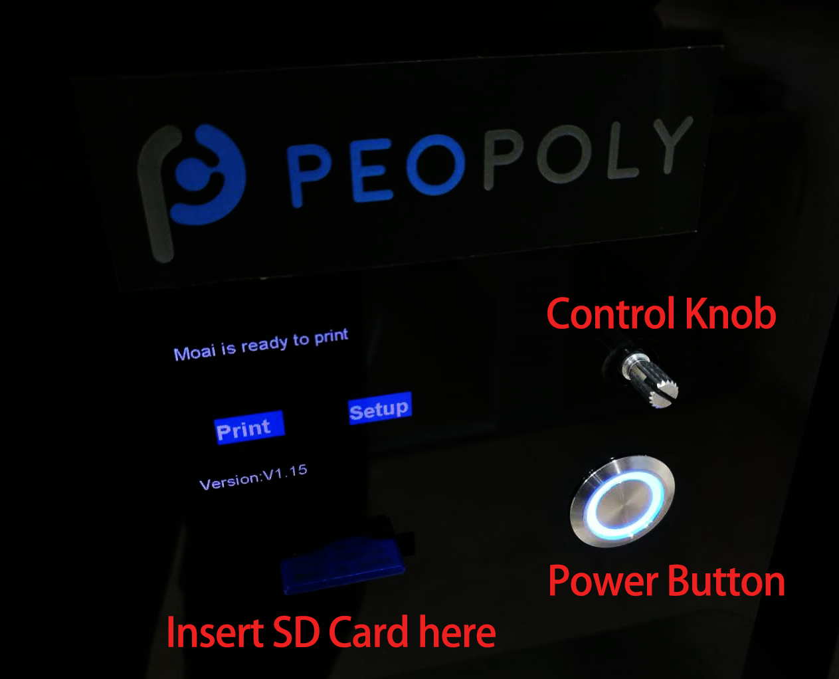
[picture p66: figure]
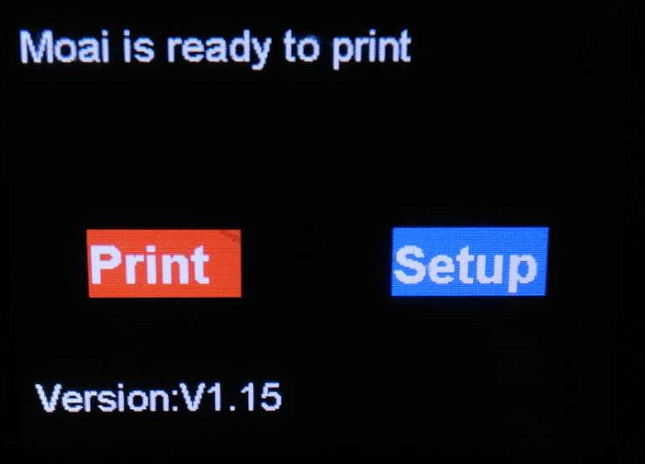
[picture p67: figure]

Select Print from the Moai’s menu and Click Confirmed.

You should see Z-Axis drops the Build Plate arm, tilt the Vat and begin to scan like below


Video: https://youtu.be/4jeJfWrDAyI

Move the paper slightly such that the circle overlaps with the laser scanning path

For additional help, use this calibration video: https://www.youtube.com/watch?v=gHHqfrhKt7M

Leveling

Since Peopoly built Moai kit to test print before shipping, the leveling should already be close to optimal. Following steps are to help you check leveling and make small changes if needed.

You should run the leveling check again when you change vats

Steps

1. Download this gcode and placed it in the SD card’s Gcode directory

https://drive.google.com/file/d/1REhwgXPzffKO1UOH15q6oeZvWlj-A3Lv/view

You will find this gcode

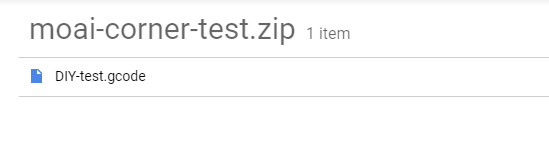
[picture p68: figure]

2. Install build plate on Moai and make sure the knob is tightened.

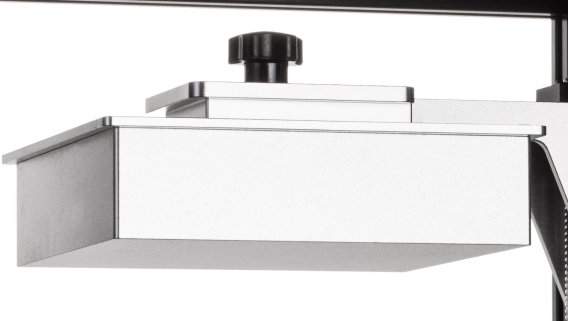
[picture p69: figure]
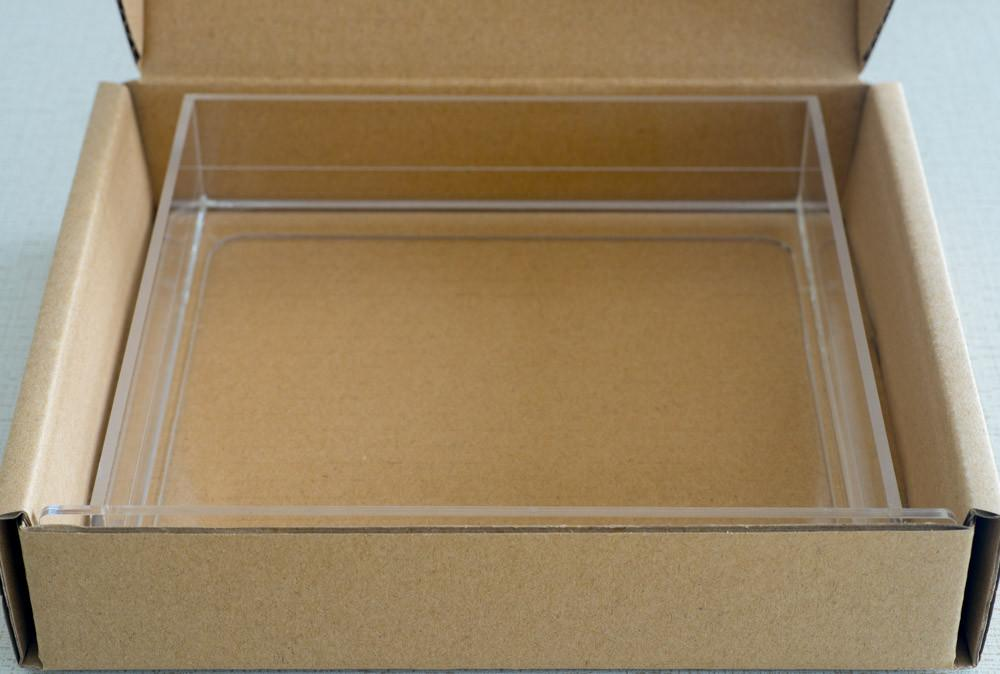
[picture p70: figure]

3. Locate the resin vat package and take out the vat. Make sure not to touch the bottom part of the vat.

4. Take out the resin bottle that looks like this:


Shake well (for about 30 seconds) before you open it and then pour resin into the vat:

The printer setup would look like:


5. Now insert the SD card in to the Moai and power it on by pressing the power button.

Print the gcode by using the control knob to

1. select print
2. Select gcode directory
3. Select DIYTest.gcode file

This print takes about 20 minutes.

This gcode contains 4 small cylinders with one at each corner of the built plate labeled as A, B, C, and D. see following pictures in Cura:


The lettering represents their location on the built plate. This helps you identify them when they are removed from the build plate.


The way to use these cylinders is that we want the printed cylinders to have a height of 10.6-10.8mm. The height of the cylinder tells us how much pressure is placed on the PDMS layer.

When the print is finished. They should look like this when build plate is facing up to the ceiling:


Check location by removing and cleaning (using Ethanol or IPA) one at the time and match them to this picture. If they don’t match, make sure you are holding the plate in the right direction.

Once you got all 4 cylinders removed and cleaned from the plate, go ahead and measure their heights and marked them by A, B, C, D.


For example, you may have A 10.4mm B 11.0mm C 10.65mm D 10.0mm

This set of numbers represents how your Moai is leveled. You can use it to help you get to optimal level (10.6 – 10.8mm) and share with those who are trying to assist you.

To adjust, first find the tools for adjustment. Locate this screwdriver from accessory box.


Then you have to remove the left and right panels and to look under the build platform and find the nuts like these.


There is one under each corner under the vat holder. The amount of adjustment to each nut is based on the difference between current cylinder height. This diagram can help you visualize better.


Using above measurements as example

To adjust A corner, find the nut under A’s corner and turn it.

Since A is off by 10.4 – 10.75 = 0.35mm. half turn tightening is 0.35mm increase in cylinder height. You make 1 half turn, and we can ex

B corner cylinder is 11mm. We can do half turn loosening of the nut to decrease the height by 0.35mm. Turning it to 10.65mm

C corner cylinder doesn’t need any adjustment

D corner is 10-10.7 = - 0.7mm. We can do a full turn of tightening of the nut to increase the height of cylinder to 10.7mm.

After adjustment, print the 4 cylinder gcode again, measure and adjust. Repeat this process until you have all 4 corners to be between 10.6 to 10.8mm

Test Print

- Download this test file:

https://drive.google.com/open?id=0Bzke6lBHG_z5ajN6VU1scll6QTQ

- Extract PM2_zring-test.gcode from the zip file


- Insert the included SD card into your computer
- Create a directory called “gcode” on the SD card
- Copy PM2_zring-test.gcode to the gcode directory created in last step
- Eject the SD card and insert it into Moai’s SD card reader
- Select Print from the Moai menu using the control knob
- Select gcode directory
- Select PM2_zring-test.gcode , and confirm to start printing

This print should last about 20 minutes and print at the B corner, see below: (disregard the four moai’s in this picture)


Couple scenarios can happen:

1. Print is successfully, print sticks to the plate and looks like the ring below:


2. Nothing is on the plate, a flattened piece can be found at the bottom of vat at the B spot
  a. Check setting to make sure laser energy is at 58
  b. The X/Y print speed is at 4
3. A partial ring is printed and seems to broken off from the middle
  a. Please increase laser energy to 59 and see if that works
4. A ring is print it but seemed to have a side of it getting cut off
  a. Please check to see if any cables are blocking laser.

Here is a link to an expanded troubleshooting chart.

https://atlas.mindmup.com/peopoly/moai_trouble_shooting/index.html

If it doesn’t work. Please redo leveling and make sure you follow the steps.

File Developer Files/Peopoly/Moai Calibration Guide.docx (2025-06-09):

Moai Calibration Check

The purpose of this guide is to verify if hardware is installed correctly and set up for printing. This guide does not deal with dimension accuracy and that is covered in a separate guide.

*Please make sure Moai is placed on a sturdy and level surface before begin working.

**FEP Vat users, most of the information still applies to you. If there is a special instruction needed for you, it will be in this green font.

These are the check steps in the order which you will do:

1. Power On
2. Setting Check
3. Galvo Scanning Test
4. Leveling
5. Test Print

Please do not pour resin into vat until the instruction tell you so or it will make testing more difficult.

Moai is shipped with galvos and plate calibrated to work together. To make sure everything is still working after delivery, we will run three tests:

1. Power on Check

DO NOT INSTALL BUILD PLATE OR PUT ANY RESIN INTO VAT for calibration test

Click the Power Switch on the Front Panel to Turn on the Machine (pic)

Two things to look for here:
- The Z Axis will raise to the top and stop at the end stop sensor
- The Vat holder will run to the top of the travel (the clicking sound is normal) and then perform a tilt action and then return to the level position


You should see this screen when Moai is ready:


2. Setting check

Use the Control Knob above the Power Switch to move between “Print” and “Setup”

Press the knob to enter “Setup” (Double press to go back)

Please check your setting and adjust to match the picture below:

If the settings do not match, you can select and click on each entry to adjust the value to match the default values.


Then use the Control Knob to scroll down to advanced_setting and click to the next screen. Check to see if the settings match this screen also.


Laser power is a key setting. We like to set it around 57-58 for Peopoly standard resin. Please check against that. Non-Peopoly resin may need to have a lower or higher laser power.

*For FEP Vat users. The Z Reset Position should be 1816


3. Galvo test

Please download following files

calibration-circle.pdf: https://drive.google.com/open?id=0Bzke6lBHG_z5MkhwQjZ0bk5UaXM

(This file is also located in your SD card’s pdf directory)

https://drive.google.com/open?id=0Bzke6lBHG_z5NmdFUmZENDZ0OEk

(This file is also located in your SD card’s gcode directory)

Print the calibration-circle.pdf and cut it to the outer square and place it in the Vat.

Insert the vat with the printed calibration-circle into the Moai.

NOTE: Make sure the Calibration Circle PDF is printed at 100% scale, do not use the Fit to page option. The dimensions of the printed box should be 5-1/8" (130.18mm), and the largest circle should be 120mm diameter.

Note how the inside squares and circles are shifted. The side with the narrow spacing should be to the back of the Moai nearest to z-axis linear rail when the vat is installed.


* For FEP vat users, use a specially made calibration file call calibration-circle FEP.pdf (https://drive.google.com/open?id=1S-L18AFP98fBC-eObGOiKP4XNvgacvXn)


Circle test Gcode:

Extract P_yuan-test.gcode from P_yuan-test.zip and place the GCode file in directory called “gcode” in a SD card.

Insert the included SD Card in the Machine (make sure you insert with the back of SD card facing up):


Select Print from the Moai’s menu and Click Confirmed.

You should see Z-Axis drops the Build Plate arm, tilt the Vat and begin to scan like below


Video: https://youtu.be/4jeJfWrDAyI

Move the paper slightly such that the circle overlaps with the laser scanning path

For additional help, use this calibration video: https://www.youtube.com/watch?v=gHHqfrhKt7M

Leveling

Since Peopoly built Moai kit to test print before shipping, the leveling should already be close to optimal. Following steps are to help you check leveling and make small changes if needed.

You should run the leveling check again when you change vats

Steps

1. Download this gcode and placed it in the SD card’s Gcode directory

https://drive.google.com/file/d/1REhwgXPzffKO1UOH15q6oeZvWlj-A3Lv/view

You will find this gcode


2. Install build plate on Moai and make sure the knob is tightened.


3. Locate the resin vat package and take out the vat. Make sure not to touch the bottom part of the vat.

4. Take out the resin bottle that looks like this:


Shake well (for about 30 seconds) before you open it and then pour resin into the vat:

The printer setup would look like:


5. Now insert the SD card in to the Moai and power it on by pressing the power button.

**FEP Vat users, please make sure your z-reset position in advanced setting is set to 1816

Print the gcode by using the control knob to

1. select print
2. Select gcode directory
3. Select DIYTest.gcode file

This print takes about 20 minutes.

This gcode contains 4 small cylinders with one at each corner of the built plate labeled as A, B, C, and D. see following pictures in Cura:


The lettering represents their location on the built plate. This helps you identify them when they are removed from the build plate.


The way to use these cylinders is that we want the printed cylinders to have a height of 10.6-10.8mm. The height of the cylinder tells us how much pressure is placed on the PDMS layer.

**FEP Vat users, instead of 10.6-10.8mm you have a wider tolerance of 10.3-10.8mm

When the print is finished. They should look like this when build plate is facing up to the ceiling:


Check location by removing and cleaning (using Ethanol or IPA) one at the time and match them to this picture. If they don’t match, make sure you are holding the plate in the right direction.

Once you got all 4 cylinders removed and cleaned from the plate, go ahead and measure their heights and marked them by A, B, C, D.


For example, you may have A 10.4mm B 11.0mm C 10.65mm D 10.0mm

This set of numbers represents how your Moai is leveled. You can use it to help you get to optimal level (10.6 – 10.8mm) and share with those who are trying to assist you.

To adjust, first find the tools for adjustment. Locate this screwdriver from accessory box.


Then you have to remove the left and right panels and to look under the build platform and find the nuts like these.


There is one under each corner under the vat holder. The amount of adjustment to each nut is based on the difference between current cylinder height. This diagram can help you visualize better.


Using above measurements as example

To adjust A corner, find the nut under A’s corner and turn it.

Since A is off by 10.4 – 10.75 = 0.35mm. half turn tightening is 0.35mm increase in cylinder height. You make 1 half turn, and we can ex

B corner cylinder is 11mm. We can do half turn loosening of the nut to decrease the height by 0.35mm. Turning it to 10.65mm

C corner cylinder doesn’t need any adjustment

D corner is 10-10.7 = - 0.7mm. We can do a full turn of tightening of the nut to increase the height of cylinder to 10.7mm.

After adjustment, print the 4 cylinder gcode again, measure and adjust. Repeat this process until you have all 4 corners to be between 10.6 to 10.8mm

Test Print

- Download this test file:

https://drive.google.com/open?id=0Bzke6lBHG_z5ajN6VU1scll6QTQ

- Extract PM2_zring-test.gcode from the zip file


- Insert the included SD card into your computer
- Create a directory called “gcode” on the SD card
- Copy PM2_zring-test.gcode to the gcode directory created in last step
- Eject the SD card and insert it into Moai’s SD card reader
- Select Print from the Moai menu using the control knob
- Select gcode directory
- Select PM2_zring-test.gcode , and confirm to start printing

This print should last about 20 minutes and print at the B corner, see below: (disregard the four moai’s in this picture)


Couple scenarios can happen:

1. Print is successfully, print sticks to the plate and looks like the ring below:


2. Nothing is on the plate, a flattened piece can be found at the bottom of vat at the B spot
  a. Check setting to make sure laser energy is at 58
  b. The X/Y print speed is at 4
3. A partial ring is printed and seems to broken off from the middle
  a. Please increase laser energy to 59 and see if that works
4. A ring is print it but seemed to have a side of it getting cut off
  a. Please check to see if any cables are blocking laser.

Here is a link to an expanded troubleshooting chart.

https://atlas.mindmup.com/peopoly/moai_trouble_shooting/index.html

If it doesn’t work. Please redo leveling and make sure you follow the steps.

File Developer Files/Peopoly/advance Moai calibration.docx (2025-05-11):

Purpose of the Guide:

Due to shipping and variations in installation, the galvos may be misaligned. The goal of this guide is to help check and calibrate the galvos correctly. Firmware version 1.16 will not completely eliminate the optical distortion that may show on the edges of the build volume and we are still working on that. The rough galvo adjustments and the finer adjustments via the X/Y Size settings should help users to print dimensionally accurate parts in the center square area of the build plate.

*This guide also works for Moai 200

Before we start, make sure you have the protection glasses ready.

NOTE: The X axis is front to back and the Y axis is left and right as you are looking at the printer from the front door.

1. Remove Left and Right side panels and Built plate

2. Set firmware settings for X/Y Size and X/Y Deviation to the default values: (critical)

http://wiki.peopoly.net/doku.php?id=moai:firmware

3. Print the calibration-circle.pdf and cut it to the outer square and place it in the Vat.

(same as the setup steps)

https://drive.google.com/open?id=0Bzke6lBHG_z5MkhwQjZ0bk5UaXM

Note how the inside squares and circles are shifted. The side with the narrow spacing should be to the back of the Moai nearest to z-axis linear rail when the vat is installed.


NOTE: Make sure the Calibration Circle PDF is printed at 100% scale, do not use the Fit to page option. The dimensions of the printed box should be 5-1/8" (130.18mm), and the largest circle should be 120mm diameter.

4. Insert the Vat with the printed calibration-circle in the Moai.

Please wear your protection glasses for next step


5. Centering with the laser. Download the center-cross gcode for Moai from here (https://drive.google.com/open?id=1MnPFxxParUH_2cQgx4YL64S05QaAm0Qi). (Moai 200 version here (https://drive.google.com/open?id=1mhBOITKgJT5DSrwv0f0InIW64FF_4-hN))It provides a crossing pattern that helps to match to the printed calibration circle’s center. The pattern looks like this:

If the center of the cross is too far away from the center of the circle, you can move the laser spot by using hex key (included in the kit) to loosen the clamping screws on galvo holder block. You can then turn the galvos by turning the motor part (where power cable is attached) to set its position while the laser is scanning the cross. Be very careful about it as a very small turn will affect the X/Y position greatly. Do not touch the mirror part of the Galov. Make sure both gavlo is pushed completely into the sockets. Y-Galvo may drop down a little when you loosen the screw. See below picture:


6. Download moai-adv-calib.zip from

https://drive.google.com/open?id=0Bzke6lBHG_z5TEE0U3k0Szhabm8

Moai 200 version here (https://drive.google.com/open?id=1vLYipN84zp2M3vhEEM2oLn17jgd8iFE_)

Extract the moai-adv-calib.gcode inside the zip file and place it in the gcode directory of the sd card

Please wear your protection glass for next step

DO NOT TOUCH TINY MIRRORS IN THE GALVO IN ANY CASE, SEE BELOW:


7. Print the moai-adv-calib.gcode.

The gcode will trace the outer larger circle of the printed calibration-circle 5 times before tracking the small circle for 15 times. It will then repeat.

While Moai is scanning the calibration circles, use a small slotted screwdriver (included in the kit) to adjust the potentiometer screw on galvo driver board so that the laser aligns to the printed circle. (Be very careful, a very small turn will have a large effect on the size of the X/Y scanning) Match the larger circle and then back to the smaller circle and vice versa until both matching closely. Once you have the scanning match the inner circle and outside the larger circle, you can stop by canceling the print. You will likely not be able to get the outside circle and the inside circle to completely match, do not stress and focus on matching the outside circle and move on to next step.


For newer galvo


8. Set Laser back to the previous level. 58 for Moai Model resin or other numbers for other resin and then Print the 20mm cube to check calibration results. Do not modify the firmware setting:

https://drive.google.com/open?id=0Bzke6lBHG_z5bEl2WjZNeHJHSUU

9. If a minor adjustment is still needed, use Asura by Peopoly software to create custom calibration profile: http://wiki.peopoly.net/doku.php?id=moai:asura

NOTE: The X-axis is front to back and the Y-axis is left and right as you are looking at the printer from the front door.

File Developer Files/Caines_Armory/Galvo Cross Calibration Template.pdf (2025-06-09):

# MOAI130 GalvoCalibrationTemplate


DOOR | DOOR

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

Usingthismethodtocenteryourgalvoswillallowyoutobeabletouse100%ofyour buildvolumeontheMOAI130.Asimilarprocesscanbeusedforthe200,dimensionspending.



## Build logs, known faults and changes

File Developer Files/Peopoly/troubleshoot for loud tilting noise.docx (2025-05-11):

Leandro,

Sorry about the trouble. The loud noise and the description of bad layer separation indicate the issue centers around the tilting and peeling action.

Steps to check

1.

Remove the the Platform cover on page 30 of

https://docs.google.com/presentation/d/1yzSxYxJ2hDWH5Tks4eD-P5XpEBOaRhRxpic4mbyX3ks/edit?usp=sharing

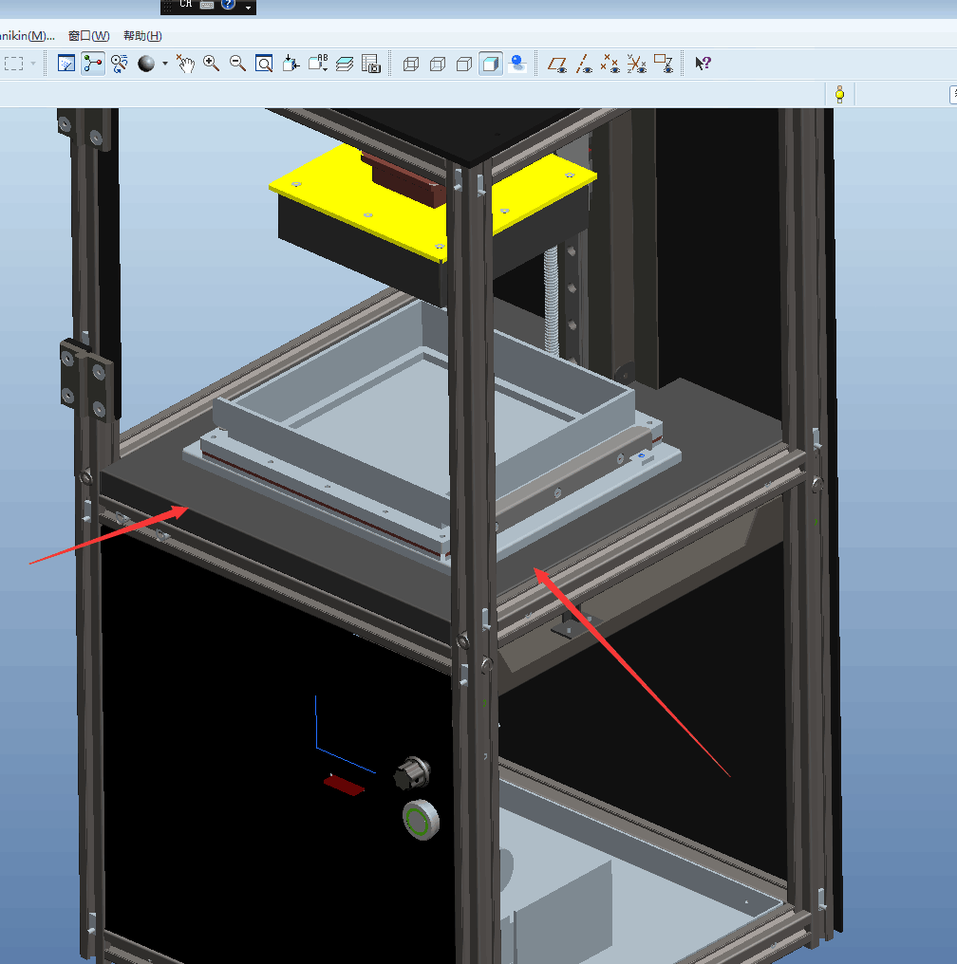
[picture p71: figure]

Run a test print with gcode at (https://drive.google.com/open?id=0Bzke6lBHG_z5ajN6VU1scll6QTQ)https://drive.google.com/open?id=0Bzke6lBHG_z5ajN6VU1scll6QTQ

(https://drive.google.com/open?id=0Bzke6lBHG_z5ajN6VU1scll6QTQ)Best do not use resin.

See if the sounds still persists, if then check

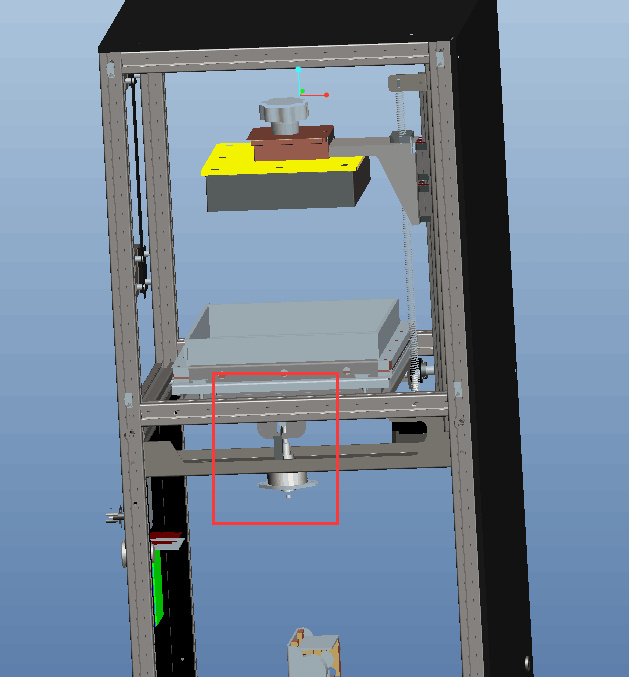
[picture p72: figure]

The most common problem centers around the little silver block and pm motor. I think we cover this and you said it is good. Just checking every key step:

On page 24. Make sure the silver metal is secured from below and from the side.

https://docs.google.com/presentation/d/1yzSxYxJ2hDWH5Tks4eD-P5XpEBOaRhRxpic4mbyX3ks/edit?usp=sharing

And it is straight like this

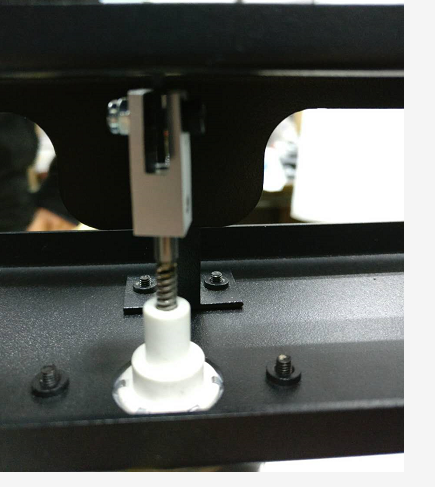
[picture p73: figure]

This is most frequent source of the problem.

And also check movements here:

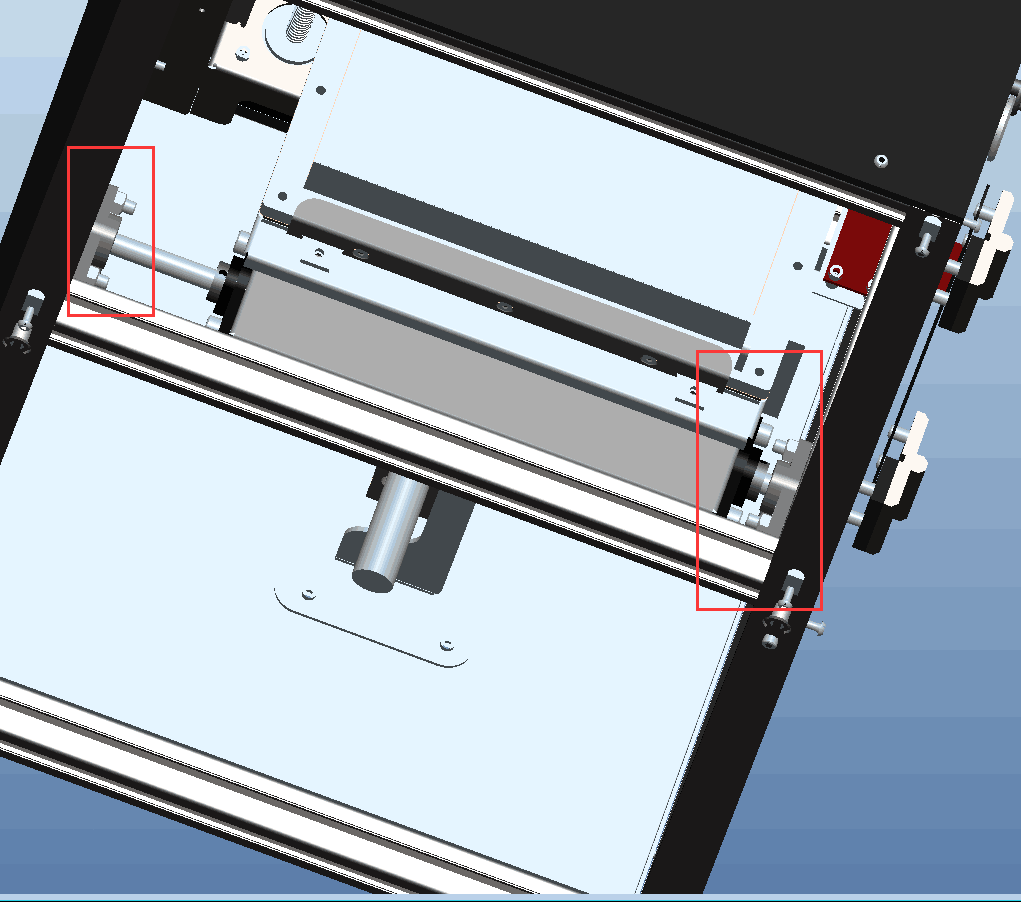
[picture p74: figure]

And see if it is secured and not moving holding platform in place while vat tiles.

If you are not sure, film both 2 silver brackets and the pm motor while the print is running and show us that.

The ultimate test is to remove pm motor and the metal hook and move the platform up down and see if you can reproduce the noise. If not, then we will replace the pm motor as the rod may have been damaged

An additional note is that your Cura and profiles may be outdated based on your Facebook pictures and comments. Infill should be 70%:

Uninstall your current Cura. Please delete this directory before installing

C:\Users\"username"\AppData\Roaming\cura

And then install this

Latest Cura:

https://drive.google.com/open?id=0Bzke6lBHG_z5cjJPNHdXaFZrWWM37

(https://drive.google.com/open?id=0Bzke6lBHG_z5cjJPNHdXaFZrWWM)

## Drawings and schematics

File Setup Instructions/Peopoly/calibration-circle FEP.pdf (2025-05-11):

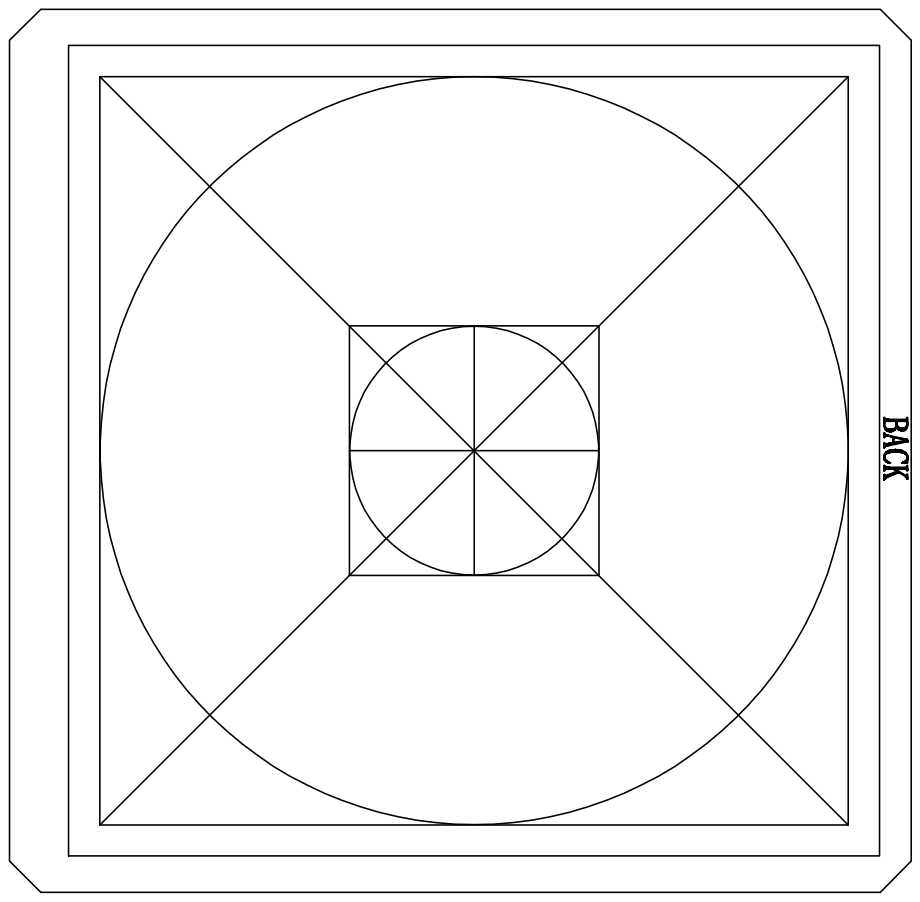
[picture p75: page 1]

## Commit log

2025-05-11 Initial Push ALL
    This is the initial push of the cumulative files for the MOAI Laser SLA printer. This includes current projects and previous developer files.
    Files over 100MB have been removed from the repository to meet push limits, these files are older software installers and the MOAI head gcode.
    [200-asuracalibration-198.stl, 200-asuracalibration.stl, 20mm-resin-saver-cube.stl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]
2025-05-14 Assembly photos
2025-06-06 Vat v12
    Higher volume vat design, easier to pour. M4-0.5 and 8-32 screw versions
    [Moai Vat High Volume 8-32.3mf, Moai Vat High Volume M4-0.5.3mf, Plexi Plate CUT Sample.3mf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]
2025-06-08 Updated slicer profiles tree
    [moai.obj]
2025-06-09 File Re-organization
    Separate development files and release files.
    Improve organization for end-users.
    Preparing for new developer contributions.
    [200-asuracalibration-198.stl, 200-asuracalibration.stl, 200-leveling-big.stl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]
2025-06-09 Organize vat photos
    [AsuraCalib1.STL, AsuraCalib2.STL, peomoai-solid.stl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]
